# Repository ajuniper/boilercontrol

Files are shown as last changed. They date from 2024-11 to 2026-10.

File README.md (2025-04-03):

# Boiler Controller

ESP32 based heating and hot water controller with LCD touchscreen, RTC, web page, temperature sensors for boiler cycling.

Being created to try to make an aging oil boiler more efficient with different target temperatures for different circuits, with setback based on outside temperature, with cooldown cycles to use the heat left in the system when the schedule is completed.
More description, photos and screenshots coming soon.

## URLs

All requests are `GET` requests (yuk!)

* `/` and `/boiler` gives current status and management controls

* `/scheduler` gives html page for setting schedules
* `/schedset?ch=X&day=D&slot=H:MM&state=01` for updating individual slots in schedules, day = 0-6=M-S, state = 0 or 1
* `/schedset?ch=X&day=D&slot=H:MM` retrieve given schedule slot
* `/schedset?ch=X&day=D` retrieve schedule for day
* `/config?name=schedule&id=N&value=X` set schedule for channel N, must be 96 0/1/2 characters

* `/heat?ch=N&q=X` manual timer for channel, where X is seconds to run (0=off, -1=forever)
* `/config?name=chactive&id=N&value=X` set channel active or inactive

* `/config?name=wuBase&id=N&value=X` set time channel starts before requested on time
* `/config?name=wuThrsh&id=N&value=X' set temp below which channel N will start early
* '/config?name=wuScale&id=N&value=X' set float scaling factor to calculate advance time from amount below threshold
* '/config?name=wuLimit&id=N&value=X' set max amount channel can advance by

* '/config?name=bstThrsh&id=N&value=X' set temp below which channel N will switch to boosted temperature

* `/config?name=orThrsh&id=N&value=X' set temp below which channel N will finish late
* '/config?name=orScale&id=N&value=X' set float scaling factor to calculate overrun time from amount below threshold
* '/config?name=orLimit&id=N&value=X' set max amount channel can extend by

* `/config?name=tgttmp&id=N` reports current target hot temperature for channel N
* `/config?name=tgttmp&id=N&value=X` sets target hot temperature for channel N
* `/config?name=tgttmp2&id=N` reports current target warm temperature for channel N
* `/config?name=tgttmp2&id=N&value=X` sets target warm temperature for channel N
* `/config?name=cooltmp&id=N&value=X` sets min cooldown temperature for channel N
* `/config?name=coolrun&id=N&valueX` sets the cooldown run time for channel N (default 120, 0 = off)
* `/config?name=circtime&id=N&valueX` sets the sludge buster max time to sit idle in seconds (default 86400 = 1 day, 0 = off)
* `/config?name=circrun&id=N&valueX` sets the sludge buster run time (default 120, 0 = off)
* `/config?name=mainsthrsh&id=N&valueX` sets the mains detection threshold for pin N (default 350, pins 34, 35 ,36, 39 )

* `/config?name=boiler&id=cyct&value=X` sets min off time for cycling boiler (default 120 seconds)
* `/config?name=boiler&id=cycpc&value=X` sets percentage which flow must drop to end cycle (default 10%)
* `/config?name=boiler&id=wait&value=X` sets time in S to wait after setting each relay (3 seconds)

* `/config?name=showbutt&id=0&value=X` enable or disable showing button regions, 1=regions+touch, 2=regionsboxed+touch, 3=2+syslog touch

Provided by the updater library:
* `/update` gives page for doing OTA updates
* `/update` use __POST__ request with body containing new firmware.bin
* `/reboot` reboots the system

Provided by tempreporter library:
* `/temperatures` reports current DS18B20 readings
* `/api?id=XXX` reports current temperature for sensor named `XXX`
* `/config?name=trremap&id=X&value=AAA+NNN+DIS` sets name of sensor `AAA` to `NNN` (where `XXX` is typically sensor MAC address), optionally disables
* `/fake?id=XXX&temp=t.tt` creates fake sensor `XXX` with value `t.tt` (used for testing)
* `/config?name=trpin&id=(18b20|dht11)[&value=N]` sets or gets the pin associated with the different sensors (reboot after to take effect)

Provided by the tempfetcher library
* `/config?name=fcst&id=rate&value=X` sets the minutes between fetching forecasts
* `/config?name=fcst&id=ahead&value=X` sets the number of hours ahead to look for lowest temperature
* `/config?name=fcst&id=behind&value=X` sets the number of hours behind to look for lowest temperature
* `/config?name=weather&id=url&value=x` sets the URL to retrieve weather forecasts from

## Expected sensor names

Need to associate specific DS18B20 with given name via the `/remap` URL above.
Max 12 characters due to preferences library limits.

* `boiler.flow` is the sensor on the output from the boiler
* `boiler.rethw` is the sensor on the return from the hot water tank
* `boiler.retht` is the sensor on the return from the main heating circuit

## Preferences objects

pin.ds18b20
pin.dht11
remap.[sensorID]
temprep.poll
temprep.submit

wifi.hostname
wifi.ssid
wifi.password

targettemp.[ch]
chactive.[ch]
warmup.[ch]
schedule.[ch]

## Scheduler web page DOM objects

* channels tabs
* days tabs
* c0 c1 (chcontent)
  * s0.0 s0.1 s0.2 ... (daycontent)
    * form (schedule)
      * 00:00 (timeslot)
      * label
        * checkbox value="hh:mm"
      * label
        * checkbox value="hh:mm"
      * label
        * checkbox value="hh:mm"
...

## configuring temperature sensors
```
curl -s 'http://boiler/config?name=trremap&id=0&value=28-ff641f79b51c46+boiler.flow+1'
curl -s 'http://boiler/config?name=trremap&id=1&value=28-ff641f79b7e8c2+boiler.rethw+1'
curl -s 'http://boiler/config?name=trremap&id=2&value=28-ff641f79b7d4df+boiler.retht+1'
```

## My House Settings

### Boiler

Extend zone valve duration a little beyond default
```
boiler.cyct = 120
boiler.cycpc = 10
boiler.wait = 5
fcst.ahead = 5
```

### Hot Water

No warm up time to be added

```
wuBase = 0
```
Advance if 0 degrees in forecast by up to 15 minutes
```
wuThrsh = 0
wuScale = 180
wuLimit = 900
```
No boost or overrun
```
bstThrsh = -100
orThrsh = -100
orScale = 0
orLimit = 0
```
Target temperature 65 degrees, only one run temperature
```
tgttmp = 65
tgttmp2 = -1
```
Only run cooldown cycle for 3 minutes or until less than 60 degrees
```
cooltmp = 60
coolrun = 180
```
Circulate daily for a minute for sludge buster
```
circtime = 86400
circrun = 60
```

### Heating

Heating always needs 45min warmup
```
wuBase = 2700
```
Extend heating by up to an hour if forecast less than 8 degrees (extra 4 minutes per degree)
```
wuThrsh = 8
wuScale = 240
wuLimit = 3600
```
Force heating hot if less than -3 degrees forecast
```
bstThrsh = -3
```
Extend heating by up to half an hour if forecast less than -3 (extra 3 minutes per degree)
```
orThrsh = -3
orScale = 180
orLimit = 1800
```
Temperatures are 50 and 65 degrees
```
tgttmp = 65
tgttmp2 = 50
```
Overrun until boiler temp is 45 or for 15 minutes
```
cooltmp = 45
coolrun = 900
```
Circulate daily for 2 minutes for sludge buster
```
circtime = 86400
circrun = 120
```

## Config backup

```
curl -s 'http://boiler/configlist' | while read a b ; do [[ $a = myconfig/* ]] || continue ; c="${a/./\&id=}" ; c="${c/myconfig\//http:\/\/boiler/config?name=}" ; v=$(curl -s "$c") ; echo "curl -s \"$c&value=$v\"" ; done

```

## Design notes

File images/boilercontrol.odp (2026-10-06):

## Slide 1

http://boiler.local/

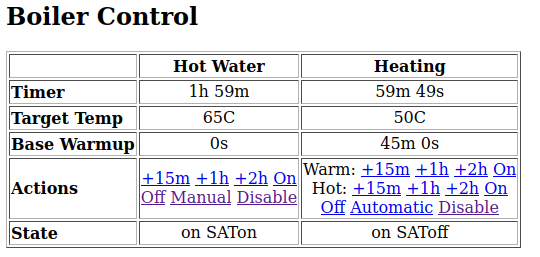
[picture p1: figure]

Time left to run

- Add 1/2/3 hours extra time
- For heating pick warm or hot
- Off will stop now but continue with next schedule
- Manual stops scheduling
- Automatic enables scheduling
- Disable turns it off completely (e.g. going away)

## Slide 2

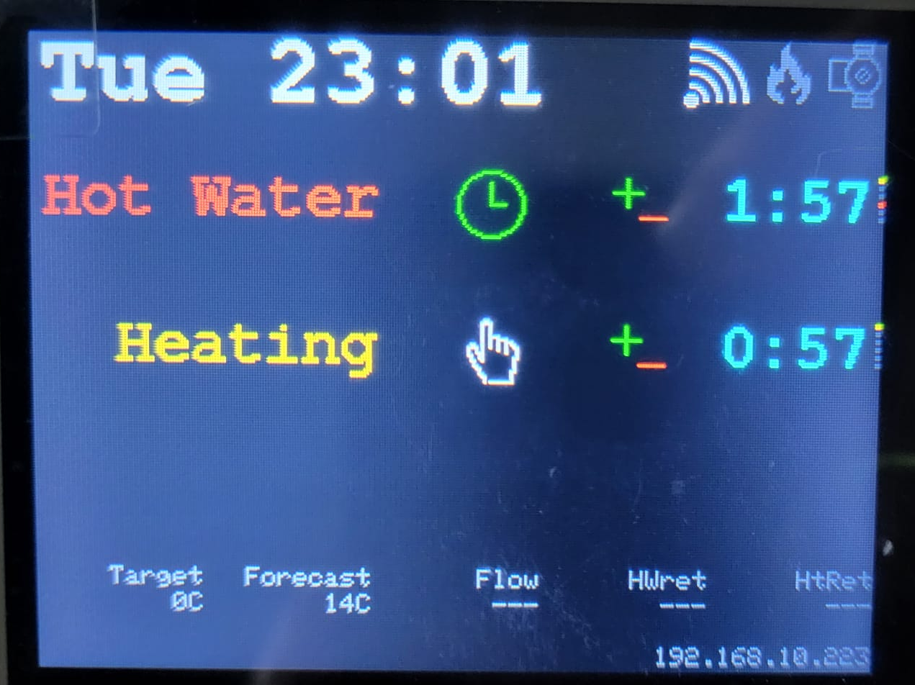
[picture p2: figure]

Enable/disable

(e.g. on holiday)

Clock = automatic

Hand = manual

No Entry = off

Orange = Low temp

Red = High temp

(set before time)

Touch and release to add 1 hour

Press and hold to turn off

Boiler and Pump

Grey = off

Blue = cooling

Red = on

Remaining time

Display goes off after 30s, touch to wake it again

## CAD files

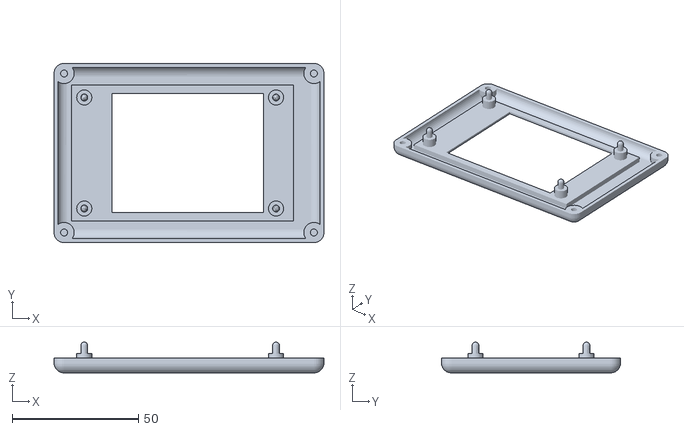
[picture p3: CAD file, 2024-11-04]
images/bezel.stl
107.0 x 71.0 x 12.2

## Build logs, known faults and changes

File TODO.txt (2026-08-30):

TEST
. coredump copy to FFS
. coredump download to set save as filename
. on/off -> off / manual / automatic
. scheduler to look at bank holidays
  https://www.gov.uk/bank-holidays.json
  https://date.nager.at/scalar/#api-version-3/tag/publicholiday/GET/api/v3/IsTodayPublicHoliday/{countryCode}
  https://date.nager.at/Api/v3/IsTodayPublicHoliday/IN?countyCode=KA
  https://api.bigdatacloud.net/data/reverse-geocode-client?latitude=51.75413&longitude=-1.124867&language=en
  https://ip-api.com/docs  http://ip-api.com/csv/?fields=countryCode,region

WIP
. add forecast lookback

FIX
. ignore input signals if corresponding output inactive
  . false triggers of ready flags
. work out how to ignore powerline noise
. wifi watchdog to restart if heating idle
  . what is behaviour of wifi reconnect?  do we get a further disconnected event?
. syslog buffer if offline
. sort PSU plug
. fix segvs
  . heating is on add hw - brownout?
  . heating is cooldown add hw - temporarily end up with not heating, not hw, pump is on
  . reduce stack sizes
  . add esp and arduino versions to /status
  . switch out syslog library
. copy-to-next does not unset existing values
. scheduler web page should cycle off warm off hot
. scheduler web page should show warmup parameters

. web show more config values
. should boost during warmup consider flow/return temp?
. should forecast tracker look at highs as well?

TODO
. button to reboot
. scheduler move day selector to LH column
. add schedule profiles
. add "if forecast temp is above X do not run"
. make web look like lcd
. scheduler onscreen
. adjust target temp based on return temp (what are the rules?  try to minimise flow based on ret+15?)
. auto hotspot if no wifi
. ntp, syslog targets from dhcp
. mqtt

IGNORE wnf
. persist on-until time in rtc/flash (scheduler fixes)
. run heating hotter for some initial period (do it manually via multi temp schedule)
# query param to avoid redirect on direct config change (new value in 302)
. watchdog timer (already there)
* target temp defaults to 0
# when web sets warm/hot, display should update
. save default config values

TESTED
rtc integration
target temperature adjustment
temperature cycling
web server
pump/boiler icon colour
1h displayed as 1:60
pump stays blue after channels go off
fake temperatures
. web
        . need newline before Hot Water 1h
        . obey channel enabled flag
        . add control for enable
. why does pump run on when HW satisfied? (icon only)
. flash persistence
. timezone not in effect
. scheduler page does not render due to JS error
. littlefs fails to open/initialize every time
. save channel active setting in flash
scheduler
    scheduler does not save to flash
    scheduler js does not load from boiler
    initialiser to read from flash
    URL to set 15 minute slot
    scheduler method to set slot & save to flash
    scheduler to obey channel active flag
    copy-to-next button
    done button
    web page to set schedule with js for toggling
link to scheduler from front page
. copy to next Sat->Sun does not work
. crashes when using copy to next / switching day
. scheduler js should use one get not 96
    bulk load of daily schedule
    correct runtime if turn on in middle of HW cycle
    URL to adjust base warmup
    scheduler does not account for time slot already partially passed
    summertime heating cycling (30s every 10 mins)
    scheduler warmup set
    correctly detect heating if turn on <warmup before schedule
. why does web say heating satisfied + satisfiedON?
. web links ok after becoming relative
. stop button should inhibit scheduler until end of current cycle
. run scheduler at reboot
. sludge buster should not run if this channel active
    sludge buster will start @5 mins
    start manual timer to overlap with sludge buster
. check scheduler behaviour if channel ready running ( for < or > time)
. web page runtime/cooldown time should be hh:mm:ss not just /60
. sludge buster should not run if other channel active (should not leave channel on off/calls/satoff)
. check uptime
. sat output should record/report state even if no pin
. changing schedule should force reevaluation
# temp labels
# invert touch screen coordinates if display_rotation=3
# target should be --- if boiler off
# fake temperatures
# mains sense inputs in reverse order
# relay outputs in wrong order
# cycle based on flow hysteresis + min cycle time
# config for boiler cycling
# config to disable tempreporter
display to show target temp
temperature fetching
. web rotate top table to show better on mobile
. test /configlist
. check display updates as expected on turn-off
# active does not load from config / save to config
# scheduler config names not documented
# schedule does not load from config / save to config (rejected by mycfg)
  (maybe try putData / getData or RLE)
# tempreporter remap config names too long
# scheduler config nodes name too long
# set full schedule to config causes segv (add printf)
. scheduler done link does not go back to home page
# lcd active does not save to config
. watchdog reboots when first starting - TR task - fixed?
. clock refresh flicker
# no clock until wifi joined
. rewire mains to boiler correctly
. relay #4 not working, LED not active
. all relays work
. if start hw then htg, htg relay does not fire
. test html pages
tempchannel to have multiple temps
        know which is in use - scheduler
        know which is in use - web
        know which is in use - display
        know temp for each
. sequence with delay boiler off, pump off, zv deactivate - not all changed in single pass, cannot deactivate zv before pump
  . test changes to sequence boiler and pump on
. weird syslog characters
. config value for 3s delay
. config for sludge buster
. test state info always present in web even if ch disabled
. if shorten schedule then need to recalculate
. if turn off during schedule then do not restart until next interval
. cycle based on return temp + min off time
. heating boost   bstThrsh(0)
. extend manual heating via web does not update target temp
tempchannel to have multiple temps
        scheduler to spot change in requested temp and adjust
. heating advance wuThrsh(12) wuScale(0) wuLimit(0)
. defer sludge if other channel is active
. heating extend  orThrsh(4) orScale(0) orLimit(0)
. when load schedule page, select current day
. refresh web page every 15s
. sludgebuster should run for shorter time than cooldown
. cooldown based on temperature
. cooltime != circtime, during circ do not check temperature
. config value for mains detect threshold
. boost temperature during warmup
. calibrate mains detectors
. adjustTimer to ignore small changes
. touch screen flaky - reflow header on LCD
. config value for mains detect INPUT_ON_MILLIS
. check ready pin behaviour states
. check that mainsdetect is happy with half wave from mid position setting
. add +15m option to web
. add status web page showing bssid, cpu%, ram, etc.
. save core dumps to flash and serve via web
. correctly pick best SSID at boot
. force reset 1wire bus if no sensors - how?
. query DS18B20 individually to make compatible with parasitic mode
. move internal cables away from display
. coredump copy to FFS
. coredump download to set save as filename

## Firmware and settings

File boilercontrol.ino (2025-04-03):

#include <mywifi.h>
#include "projectconfig.h"
#include <AsyncTCP.h>
#include "time.h"
#include <WiFiUdp.h>
#include <mysyslog.h>
#include "pinconfig.h"
#include "display.h"
#include "tempsensors.h"
#include "mytime.h"
#include "outputs.h"
#include <tempreporter.h>
#include <mywebserver.h>
#include <webupdater.h>
#include <myconfig.h>
#include "scheduledoutput.h"
#include "buttons.h"
#include <mysystem.h>

// task to update outputs
static TaskHandle_t outputtask_handle = NULL;

// last output state
ScheduledOutput o_pump_on;
ScheduledOutput o_boiler_on;
t_output_state o_boiler_state;
t_output_state o_pump_state;
int target_temp = 999;

#include <my_secrets.h>
const char* ssid     = MY_WIFI_SSID;
const char* password = MY_WIFI_PASSWORD;

// if we cycle the boiler off at its target temperature
// then we can't start it again for this period
#ifdef SHORT_TIMES
#define BOILER_SHORT_CYCLE 30
#else
#define BOILER_SHORT_CYCLE 120
#endif
#define BOILER_RELAY_WAIT 3

//////////////////////////////////////////////////////////////////////////////
//
// Heat channel objects
#include "heatchannel.h"

//////////////////////////////////////////////////////////////////////////////
//
// Web Server Stuff
#include "webserver.h"

static const char * handleConfigBoiler(const char * name, const String & id, int &value) {
    if (id == "cyct") {
        // all ok, save the value
        return NULL;
    } else if (id == "cycpc") {
        // all ok, save the value
        return NULL;
    } else if (id == "wait") {
        // all ok, save the value
        return NULL;
    } else {
        return "boiler config not recognised";
    }
}


//////////////////////////////////////////////////////////////////////////////
//
// setup

void setup() {
    // put your setup code here, to run once:
    // Serial port for debugging purposes
    Serial.begin(115200);
    Serial.println("Starting...");
    MyCfgInit(true);
    MyCfgRegisterInt("boiler", &handleConfigBoiler);

    mytime_setup(MY_TIMEZONE, PIN_RTC_CLK, PIN_RTC_DATA, PIN_RTC_RST);
    WIFI_init("boiler");
    SyslogInit("boiler");
    xTaskCreate(output_task, "outputs", 10000, NULL, 1, &outputtask_handle);
    webserver_setup();
    SYS_init();
    tempsensors_init();
    heatchannel_setup();
    buttons_init();

    // start the display update task
    display_init();

    // firmware updates
    UD_init(server);
}

//////////////////////////////////////////////////////////////////////////////
//
// output control
// separate task to permit mains cycle sync

static void output_task (void *)
{

    // set up digital IO - set output state before setting mode to avoid boot time glitches
    digitalWrite(PIN_O_PUMP_ON, RELAY_OFF);
    digitalWrite(PIN_O_BOILER_ON, RELAY_OFF);
    pinMode(PIN_O_PUMP_ON, OUTPUT);
    pinMode(PIN_O_BOILER_ON, OUTPUT);

    delay(1000);

    // cache the requested output settings
    // only update when we are signalled
    bool last_boiler = false;
    bool this_boiler = false;
    bool this_pump = false;
    int last_target_temp = target_temp;
    time_t boiler_cycle_time = 0;
    int hysteresis = 100 - 10;
    int i;
    bool need_suspend = false;
    bool last_suspend;

    while(1) {
        // wait for signal
        uint32_t n = 0;
        while (n == 0) {
            TickType_t waittime = 5*1000; // 5s
            time_t now = time(NULL);
            int flow_temp = tempsensors_get("boiler.flow");

            this_boiler = o_boiler_on.checkState(now);
            if (last_boiler != this_boiler) {
                if (this_boiler == true) {
                    syslogf(LOG_DAEMON | LOG_WARNING, "Boiler can fire, temp now %dC",tempsensors_get("boiler.flow"));
                }
                last_boiler = this_boiler;
                boiler_cycle_time = 0;
            }

            last_suspend = need_suspend;
            need_suspend = false;
            for (i=0; i<num_heat_channels; ++i) {
                need_suspend |= channels[i].isChanging(now);
            }
            if (need_suspend != last_suspend) {
                if (need_suspend) {
                    syslogf(LOG_DAEMON|LOG_WARNING, "Suspending pump and boiler for valve change");
                } else {
                    syslogf(LOG_DAEMON|LOG_WARNING, "Resuming pump and boiler after valve change");
                }
            }

            // recalculate whether the boiler should be running or not
            // this is where we are cycling the boiler to temperature
            if (this_boiler == false) {
                // boiler is requested off
                boiler_cycle_time = 0;
                waittime = 3600 * 1000; // 1hr
                o_boiler_state = OUTPUT_OFF;

            } else if (need_suspend) {
                // zone valves are changing, we should turn pump and boiler off
                waittime = 1000; // 1s
                o_boiler_state = OUTPUT_OFF; // OUTPUT_SUSPEND
                this_boiler = false;
            } else if (boiler_cycle_time > now) {
                // boiler is already cycled off by time so nothing to do
                // just wait until the end of the cycle window unless
                // something changes in the mean time
                waittime = (boiler_cycle_time - now) * 1000;
                this_boiler = false;

            } else if ((boiler_cycle_time != 0) &&
                       (flow_temp > ((last_target_temp * hysteresis)/100))) {
                // boiler is cycled off by temperature so nothing to do
                // just wait a few seconds and check again unless
                // something changes in the mean time
                waittime = 10000;
                this_boiler = false;

            } else if (flow_temp > last_target_temp) {
                // boiler just went over temperature

                // read the cycling config
                int short_cycle = MyCfgGetInt("boiler","cyct", BOILER_SHORT_CYCLE);
                hysteresis = 100 - MyCfgGetInt("boiler","cycpc", 10);

                syslogf(LOG_DAEMON | LOG_WARNING, "Cycling boiler off, flow temp %dC is greater than target %dC fire again at %dC",flow_temp,last_target_temp,((last_target_temp * hysteresis)/100));

                // start a new cycle period
                this_boiler = false;

                // the earliest time the boiler can fire again
                boiler_cycle_time = now + short_cycle;

                // how long to wait before looking again
                waittime = short_cycle * 1000;

                // we are cycling the boiler
                o_boiler_state = OUTPUT_COOLING;

            } else {
                // boiler should be on
                o_boiler_state = OUTPUT_HEATING;
                if (boiler_cycle_time != 0) {
                    // boiler just finished cycling
                    syslogf(LOG_DAEMON | LOG_WARNING, "Cycling boiler back on, temp now %dC",flow_temp);
                    boiler_cycle_time = 0;
                }
            }

            // calculate what the pump should be doing
            if (need_suspend) {
                // pump should be off for zv change
                this_pump = false;
                o_pump_state = OUTPUT_OFF; // OUTPUT_SUSPEND
            } else if (o_pump_on.checkState(now)) {
                this_pump = true;
                // update what the pump is doing
                // if boiler is on or cycling then we are heating
                o_pump_state = (o_boiler_state == OUTPUT_OFF)?OUTPUT_COOLING:OUTPUT_HEATING;
            } else {
                // pump is not on
                this_pump = false;
                o_pump_state = OUTPUT_OFF;
            }

            // update the outputs
            digitalWrite(PIN_O_PUMP_ON, this_pump?RELAY_ON:RELAY_OFF);
            digitalWrite(PIN_O_BOILER_ON, this_boiler?RELAY_ON:RELAY_OFF);

            for (i=0; i<num_heat_channels; ++i) {
                if (channels[i].setOutputPin(now)) {
                    waittime = min((TickType_t(500)), waittime);
                }
                if (channels[i].setSatisfiedPin(now)) {
                    waittime = min((TickType_t(500)), waittime);
                }
            }

            // if change is coming then be ready for it
            if (o_boiler_on.nextChange() > 0) {
                waittime = min((TickType_t(500)), waittime);
            }
            if (o_pump_on.nextChange() > 0) {
                waittime = min((TickType_t(500)), waittime);
            }
            // wait for something to change, either demand state or
            // calculated time period elapsed
            n = ulTaskNotifyTake( pdTRUE, pdMS_TO_TICKS( waittime) );

            // n==0 indicates timeout, else signalled
        } // end of wait for signal/timeout

        // drop out of loop if signalled that demand state changed
        last_target_temp = target_temp;
        if (last_target_temp == 999) { last_target_temp = 0; }
    }
}

//////////////////////////////////////////////////////////////////////////////
//
// main loop

void loop() {
    time_t now = time(NULL);
    unsigned long millinow = millis();
    bool changed = false;
    int i;
    BaseType_t xHigherPriorityTaskWoken = pdFALSE;

    // check timers
    for(i=0; i<num_heat_channels; ++i) {
        if (channels[i].updateTimers(now,millinow)) {
            changed |= true;
            syslogf(LOG_DAEMON|LOG_INFO,"%s triggered change",channels[i].getName());
        }
    }

    if (changed) {
        bool calling = false;
        target_temp = 0;

        // cache the interval between relay changes
        time_t relaywait = MyCfgGetInt("boiler","wait", BOILER_RELAY_WAIT);

        // see what is ready for action
        for (i=0; i<num_heat_channels; ++i) {
            if (channels[i].wantFire()) {
                calling |= true;
            }
        }
        // 999 is rendered as --- on the display
        if (target_temp == 0) { target_temp = 999; }
        if (calling) {
            // something is calling for heat
            int tt = 0;

            // action the ZV relays
            // if we get to this loop then something IS calling for fire
            // cool down is not possible if something is calling for fire
            // TODO temporary disable pump and boiler while relays change
            // TODO can we detect change in progress by output != input?
            for (i=0; i<num_heat_channels; ++i) {
                // we must set satisfied to indicate to not send heat to this channel
                // if the channel is satisfied or this channel is not asking for heat
                // (which can include cooldown too)
                // these changes are start-of-sequence so happen immediately
                bool satNew = (!channels[i].canFire()) || channels[i].isSatisfied();
                bool runNew = channels[i].wantFire();
                // sequence the requests so that we do not have a temporary contradiction
                // must not have both sat and run set
                // if sat is turning on and we are already running then turn off run first
                // and vice versa
                if (satNew) {
                    // must turn run off first
                    channels[i].setOutput(runNew,now+1);
                    channels[i].setSatisfied(satNew,now+2);
                } else {
                    // must turn sat off first
                    channels[i].setSatisfied(satNew,now+1);
                    channels[i].setOutput(runNew,now+2);
                }
            }

            // turn the pump and boiler on as required
            for (i=0; i<num_heat_channels; ++i) {
                if (channels[i].wantFire()) {
                    syslogf(LOG_DAEMON|LOG_INFO,"%s is ready",channels[i].getName());
                    // have to wait for ack from zv before firing
                    if (channels[i].canFire()) {
                        // something is asking for heat
                        tt = max(tt, channels[i].targetTemp());
                        // give the pump and boiler time for the zv to be in place
                        o_pump_on.setState(true, now+relaywait);
                        o_boiler_on.setState(true,now+relaywait+relaywait);
                        syslogf(LOG_DAEMON | LOG_WARNING, "Run pump and boiler to %dC",tt);
                    }
                }
            }
            target_temp = tt;

        } else {
            // nothing asking for heat, what about cooldown?
            calling = false;
            for (i=0; i<num_heat_channels; ++i) {
                if (channels[i].wantCooldown()) {
                    calling |= true;
                }
            }

            if (calling) {
                // something is asking for cooldown
                // this ensures other ZVs are closed

                // action the ZV relays
                // if we get to this loop then something IS calling for cooldown
                // and nothing is calling for heat
                // TODO temporary disable pump and boiler while relays change
                for (i=0; i<num_heat_channels; ++i) {
                    // we must set satisfied to indicate to not send heat to this channel
                    // if the channel is satisfied or this channel is not asking for heat
                    // (which can include cooldown too)
                    // these changes are start-of-sequence so happen immediately
                    bool satNew = channels[i].isSatisfied();
                    bool runNew = channels[i].wantCooldown();
                    // sequence the requests so that we do not have a temporary contradiction
                    // must not have both sat and run set
                    // if sat is turning on and we are already running then turn off run first
                    // and vice versa
                    // scrub that
                    // if we are now satisfied then we must enable satisfied to
                    // stop sending hw to tank at mpzv before we close the tank zv
                    // ditto v.v. if we are not satisfied (i.e. want heat to tank)
                    // then we must turn on tank zv to permit flow before we
                    // disable the satisfied output to permit tank flow from mpzv
                    if (!satNew) {
                        // want heat to tank
                        // must turn run off first
                        channels[i].setOutput(runNew,now);
                        channels[i].setSatisfied(satNew,now+1);
                    } else {
                        // do not want heat to tank
                        // must turn sat off first
                        channels[i].setSatisfied(satNew,now);
                        channels[i].setOutput(runNew,now+1);
                    }
                }

                // and set the pump/boiler
                // boiler defaults to off anyway, pump should already be on
                for (i=0; i<num_heat_channels; ++i) {
                    if (channels[i].wantCooldown()) {
                        syslogf(LOG_DAEMON|LOG_INFO,"%s is ready for cooldown",channels[i].getName());
                    }
                }

                syslogf(LOG_DAEMON | LOG_WARNING, "Run pump for cooldown");
                o_boiler_on.setState(false);
                o_pump_on.setState(true,now+relaywait);
            } else {
                // nothing on

                o_boiler_on.setState(false);
                // give the boiler a chance to stop before stopping the pump
                o_pump_on.setState(false,now+relaywait);

                // action the satisfied relays to off, not needed
                int d=0;
                for (i=0; i<num_heat_channels; ++i) {
                    channels[i].setSatisfied(false,now+relaywait+relaywait+(d++));
                }

                // action the zone valves to off
                for (i=0; i<num_heat_channels; ++i) {
                    channels[i].setOutput(false,now+relaywait+relaywait+(d++));
                }

                syslogf(LOG_DAEMON | LOG_WARNING, "Pump and boiler off");
            }
        }

        // set system outputs - via task to deal with mains sync
        // TODO should setting outputs be synchronised with setting outputs
        xTaskNotifyGive( outputtask_handle );

    } // end of something changed

    // wait a while
    delay(50);
}

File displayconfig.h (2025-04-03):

//////////////////////////////////////////////////////////////////
//
// config for display layout and behaviour
#pragma once


#include "projectconfig.h"
#include "time.h"

#ifdef display_conns_on_left
// if connections are on left then
// display (0,0) is bottom right
// touch (0,0) is top right
#define display_rotation 3
#else
// if connections are on right then
// display (0,0) is top left
// touch (0,0) is bottom left
#define display_rotation 1
#endif
#define display_max_x 320
#define display_max_y 240

// coordinate values below assume
// display (0,0) is top left

// millisecods
#define touch_delay 25
// microseconds
#define touch_release_debounce 100000
#define fontnum 1
#define clock_font &FreeMonoBold18pt7b
#define clock_x 190
#define clock_y 1
#define clock_colour TFT_WHITE
#define button_expand 10
#define display_sleep 30
#define display_brightness 200

#define channel_font &FreeMonoBold12pt7b
#define channel_x 130
#define channel_y 50
#define channel_spacing 55
#define channel_icon_size 24
#define channel_colour TFT_CYAN
#define channel_colour_hot TFT_RED
#define channel_colour_warm TFT_ORANGE
#define channel_label_x 1
#define channel_label_w channel_x
#define channel_active_x (channel_x + 30)
#define channel_active_w channel_icon_size
#define channel_timer_x (channel_x + 86)
#define channel_timer_w channel_icon_size
#define channel_countdown_x 215
#define channel_countdown_w 98
#ifdef SHORT_TIMES
#define timer_increment 10
#else
#define timer_increment 3600
#endif

#define temp_font nullptr
#define temp_x 64
#define temp_y 210
#define temp_colour TFT_DARKGREY

#define ip_font nullptr
#define ip_x 320
#define ip_y 230
#define ip_colour TFT_DARKGREY

#define pump_x 296
#define pump_y 0
#define pump_w 24
#define pump_h 24
#define pump_colour TFT_RED
#define pump_colour2 TFT_BLUE
#define pump_colour3 TFT_MAROON

#define flame_x 270
#define flame_y 0
#define flame_w 24
#define flame_h 24
#define flame_colour TFT_RED
#define flame_colour2 TFT_BLUE
#define flame_colour3 TFT_MAROON

#define wifi_x 225
#define wifi_y 0
#define wifi_w 45
#define wifi_h 40
#define wifi_colour 0xffff

#define rssi_width 24
#define rssi_height 24
#define rssi_spacing 5
#define rssi_x 246
#define rssi_y 22
#define rssi_deg 45
#define rssi_width 1
#define rssi_direction 225
#define rssi_colour TFT_LIGHTGREY

#define heat_io_x 318
//#define heat_io_x 290
#define heat_io_size 2

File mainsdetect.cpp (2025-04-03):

//////////////////////////////////////////////////////////////////////////////
//
// Mains detection objects
#include <Arduino.h>
#include "projectconfig.h"
#include "mainsdetect.h"
#include <mysyslog.h>
#include "myconfig.h"
#include <map>

// input processing stuff
// debounce interval
#define I_DEBOUNCE 100
// min distance from 0v to treat as "on"
#define INPUT_ON_LIMIT 350
// smoothing for mains frequency - only look for volts for max 1/2 cycle
#define MAINS_HZ 50
#define INPUT_ON_MILLIS (1000/(MAINS_HZ*2))

std::map<int, MainsDetect*> detectors;

static const char * cfg_set_threshold(const char * name, const String & id, int &value) {
    int i = id.toInt();
    std::map<int, MainsDetect*>::iterator j = detectors.find(i);
    if (j == detectors.end()) {
        return "Unknown pin";
    }
    if (strcmp(name, "mainsthrsh") == 0) {
        j->second->setThreshold(value);
    } else if (strcmp(name, "mainsticks") == 0) {
        j->second->setTicks(value);
    } else if (strcmp(name, "mainsdbnc") == 0) {
        j->second->setDebounceT(value);
    } else {
        return "Invalid selector";
    }
    return NULL;
}

static bool need_initialise = true;
static void initialise() {
    need_initialise = false;
    MyCfgRegisterInt("mainsthrsh",&cfg_set_threshold);
    MyCfgRegisterInt("mainsticks",&cfg_set_threshold);
    MyCfgRegisterInt("mainsdbnc",&cfg_set_threshold);
}

MainsDetect::MainsDetect(int a_pin, const char * a_name1, const char * a_name2) :
    m_pin(a_pin),
    m_name1(a_name1),
    m_name2(a_name2),
    m_zerov(-1),
    m_debounce(0),
    m_pinstate(0),
    m_state(false),
    m_disabled(true),
    m_threshold(INPUT_ON_LIMIT),
    m_ticks(INPUT_ON_MILLIS),
    m_debounce_t(I_DEBOUNCE)
{
    //calibrate();
    detectors[a_pin] = this;
}

// calibrate the zero volts level
void MainsDetect::calibrate() {
    m_disabled = true;
    if (m_pin == -1) { return; }
    char t2[100];

    if (need_initialise) {
        initialise();
    }
    m_threshold = MyCfgGetInt("mainsthrsh", String(m_pin), INPUT_ON_LIMIT);
    m_ticks = MyCfgGetInt("mainsticks", String(m_pin), INPUT_ON_MILLIS);
    m_debounce_t = MyCfgGetInt("mainsdbnc", String(m_pin), I_DEBOUNCE);

#ifdef MAINSDETECT_TESTMODE
    m_disabled = false;
    pinMode(m_pin, INPUT);
    sprintf(t2,"input pin %d in digital mode",m_pin);
    Serial.println(t2);
#else
    // calculate the average voltage to determine base level
    int a;
    int j;
    a=0;
    // twice as first pass gives bogus results
    for(j=0; j<(1000/MAINS_HZ); ++j) {
        a+=analogRead(m_pin);
    }
    a=0;
    for(j=0; j<(1000/MAINS_HZ); ++j) {
        a+=analogRead(m_pin);
    }
    // calculate the average
    m_zerov=a/j;
    //sprintf(t2,"Av for pin %d is %d\n",m_pin,m_zerov);
    //Serial.print(t2);
    if (m_zerov < 1500) {
        // not there, disable
        // TODO watch for pin coming back?
        //sprintf(t2,"disabled pin %d zerov %d",m_pin,m_zerov);
        //Serial.println(t2);
    } else {
        m_disabled = false;
    }
#endif
}

// refresh the state of the pin (every millisecond)
void MainsDetect::checkstate() {
    if (m_disabled) { return; }

#ifdef MAINSDETECT_TESTMODE
    // test mode, just do digital read
    // pull DOWN to activate
    if (digitalRead(m_pin)==0) {
#else
    int j = analogRead(m_pin);
    if ((j < (m_zerov-m_threshold)) || (j > (m_zerov+m_threshold))) {
#endif
        // mains is on, reset counter, start debounce if required
        if (m_pinstate == 0) {
            // trigger change check after debounce
            m_debounce = millis();
        }
        m_pinstate = m_ticks;
    } else {
        // mains is off, decrement counter
        if (m_pinstate > 0) {
            m_pinstate--;
            if (m_pinstate == 0) {
                // trigger change check after debounce
                m_debounce = millis();
            }
        }
    }
}

// check for debounce expiry and report if changed
bool MainsDetect::updatepin(unsigned long a_millinow) {
    // sets changed to true if value changed
    if (m_pin == -1) { return false; }
    unsigned long debounce;
    if (((debounce = m_debounce) > 0) &&
        ((a_millinow - debounce) > m_debounce_t)) {
        m_debounce = 0;
        bool x = (m_pinstate > 0);
        if (x != m_state) {
            // only action a change if it changed
            m_state = x;
            syslogf(LOG_DAEMON | LOG_INFO, "%s %s input %s",m_name1,m_name2,m_state?"set":"cleared");
            return true;
        }
    }
    return false;
}

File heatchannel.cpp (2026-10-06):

//////////////////////////////////////////////////////////////////////////////
//
// Heat channel objects
#include <Arduino.h>
#include "projectconfig.h"
#include "pinconfig.h"
#include "heatchannel.h"
#include "displayconfig.h"
#include "display.h"
#include "myconfig.h"
#include <ESPAsyncWebServer.h>
#include "tempsensors.h"
#include "finger.h"

#include <mysyslog.h>

#ifdef SHORT_TIMES
#define HEAT_COOLDOWN 30
#define HEAT_SETBACK 60
#define HEAT_SUSPEND 5
#else
#define HEAT_COOLDOWN 600
#define HEAT_SETBACK (45*60)
#define HEAT_SUSPEND 15
#endif


HeatChannel::HeatChannel(
    int a_id,
    const char * a_name,
    int a_pin_o_zv,
    int a_pin_o_zv_satisfied,
    int a_pin_i_zv_ready,
    int a_pin_i_zv_satisfied,
    int a_target_temp1,
    int a_target_temp2,
    bool a_enabled,
    int a_cooldown_duration,
    int a_cooldown_mintemp,
    int a_y,
    int a_setback
) : m_id(a_id),
    m_name(a_name),
    m_pin_zv(a_pin_o_zv),
    m_pin_zv_satisfied(a_pin_o_zv_satisfied),
    m_ready(a_pin_i_zv_ready,a_name,"ready"),
    m_satisfied(a_pin_i_zv_satisfied,a_name,"satisfied"),
    m_target_temp1(a_target_temp1),
    m_target_temp2(a_target_temp2),
    m_enabled(a_enabled),
    m_active(CHANNEL_OFF),
    m_cooldown_duration(a_cooldown_duration),
    m_cooldown_mintemp(a_cooldown_mintemp),
    m_cooldown_target(0),
    m_sludge_duration(120),
    m_endtime(0),
    m_cooldown_time(0),
    m_zv_output(false),
    m_zv_satisfied_output(false),
    m_changed(true), // trigger output setup first time around
    m_scheduler(*this, a_setback),
    m_suspendUntil(0),
    m_suspend_duration(HEAT_SUSPEND),
    m_y(a_y)

{
    if (m_pin_zv > -1) {
        digitalWrite(m_pin_zv, RELAY_OFF);
        pinMode(m_pin_zv, OUTPUT);
    }
    if (m_pin_zv_satisfied > -1) {
        digitalWrite(m_pin_zv_satisfied, RELAY_OFF);
        pinMode(m_pin_zv_satisfied, OUTPUT);
    }
}

// update timer states
// returns true if something changed
// timer or inputs
bool HeatChannel::updateTimers(time_t now, unsigned long millinow) {
    bool ret = m_changed;
    m_changed = false;
    if ((m_endtime > 0) || (m_endtime == CHANNEL_TIMER_SLUDGE)) {
        if (now > m_endtime) {
            // time to turn off
            const char * c = "";
            if (m_endtime == CHANNEL_TIMER_SLUDGE) {
                if (m_sludge_duration > 0) {
                    m_cooldown_target = -99999;
                    m_cooldown_time = now + m_sludge_duration;
                    c = ", starting sludgebuster";
                }
            } else {
                if (m_cooldown_duration > 0) {
                    m_cooldown_target = m_cooldown_mintemp;
                    m_cooldown_time = now + m_cooldown_duration;
                    c = ", starting cooldown";
                }
            }
            m_endtime = 0;
            m_lastTime = now;
            syslogf(LOG_DAEMON|LOG_INFO,"%s turning off%s",m_name,c);
            ret = true;
        }
    }
    if (m_cooldown_time > 0) {
        if (now > m_cooldown_time) {
            // time to turn off
            m_cooldown_time = 0;
            m_lastTime = time(NULL);
            syslogf(LOG_DAEMON|LOG_INFO,"%s cooldown finished",m_name);
            ret = true;
        } else if (tempsensors_get("boiler.flow") < m_cooldown_target) {
            // cooldown flow is low enough, turn off
            m_cooldown_time = 0;
            m_lastTime = time(NULL);
            syslogf(LOG_DAEMON|LOG_INFO,"%s cooldown finished early",m_name);
            ret = true;
        }
    }
    if (m_enabled) {
        ret |= m_ready.updatepin(millinow);
        ret |= m_satisfied.updatepin(millinow);
    }
    return ret;
}
void HeatChannel::adjustTimer(int dt) {
    switch (dt) {
        case CHANNEL_TIMER_OFF:
            // turn off
            if (m_endtime != 0) {
                // channel is running so set end time to
                // a moment ago
                m_scheduler.turnedOff(m_endtime);
                m_endtime = time(NULL)-1;
            } else if (m_cooldown_time != 0) {
                // channel is already off, cancel cooldown
                m_cooldown_time = time(NULL)-1;
            }
            break;
        case CHANNEL_TIMER_ON:
            // turn on
            m_cooldown_time = 0;
            m_endtime = dt;
            break;
        case CHANNEL_TIMER_SLUDGE:
            // run cooldown cycle to circulate sludge
            // TODO set m_endtime to 1/2 and check for this in updateTimers
            m_cooldown_time = 0;
            m_endtime = dt;
            break;
        default:
            // turn on for given seconds
            m_cooldown_time = 0;
            if (dt < 1000000000) {
                // delta
                if ((m_endtime == 0) || (m_endtime == CHANNEL_TIMER_SLUDGE)) {
                    // currently off so calculate absolute off time
                    m_endtime = time(NULL) + dt;
                } else if (m_endtime == CHANNEL_TIMER_ON) {
                    // noop, already fixed on
                } else {
                    // at some arbitrary value, add the extra time
                    m_endtime += dt;
                }
            } else {
                // absolute value, just save it
                m_endtime = dt;
            }
    }
    syslogf(LOG_DAEMON | LOG_INFO, "%s set to %d",m_name,m_endtime);
    m_changed = true;
    // update the last activity time here to hold off the sludge buster otherwise the sludge
    // buster triggers before the main task stops the burner
    m_lastTime = time(NULL);
}

// set the output state to the zv
// returns true if state changes
bool HeatChannel::setOutput(bool state, time_t when) {
    if ((m_enabled == false ) || (m_pin_zv == -1)) {
        return false;
    }
    bool changed = false;
    if (state != m_zv_output.setState(state,when)) {
        syslogf(LOG_DAEMON | LOG_INFO, "%s request output set to %s at %d",m_name,state?"on":"off",when);
        changed = true;
        needSuspend();
    }
    return changed;
}
bool HeatChannel::setSatisfied(bool state, time_t when) {
    if ((m_enabled == false ) || (m_pin_zv_satisfied == -1)) {
        return false;
    }
    bool changed = false;
    if (state != m_zv_satisfied_output.setState(state,when)) {
        syslogf(LOG_DAEMON | LOG_INFO, "%s request satisfied set to %s at %d",m_name,state?"on":"off",when);
        changed = true;
        needSuspend();
    }
    return changed;
}
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

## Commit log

2023-07-16 assign pin for 1wire
2023-07-16 print --- if temp not available
2023-07-16 get wrapper to find sensor to query
2023-07-16 add target temperature support
2023-07-29 configurable target temperatures
2023-07-30 add cooling cycle support
    fix some race conditions when adjusting timer
    [heatchannel.cpp]
2023-08-05 add done button and copy-to-next
2023-09-26 fix 1h shown as 1h60m
    [heatchannel.cpp]
2023-09-30 update pump colour when pump finished
2023-10-02 add log if fail to init littlefs
    [heatchannel.cpp]
2023-10-13 add updates, fix cycling, fix pump icon
    [boilercontrol.ino]
2023-10-15 fix a load of stuff
    [boilercontrol.ino, display.cpp, displayconfig.h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]
2023-10-17 persist heat channel active to flash
2023-11-05 fix problems
    web and scheduler didnt agree on which is day 0
    fix scheduling issues if scheduled mid slot
    save warmup time to flash
2023-11-11 do not run cooldown if other other channel heating
2023-11-11 maintain satisfied output state if no pin
2023-12-19 switch to use preferences library
2024-03-27 rotate display, add multitemp
    add support for display the other way up
    add support for multiple flow temps by clicking label
2024-03-27 add rotation, fix temp positioning
    [display.cpp]
2024-03-27 rotate display, flow temp select, move temps
2024-03-27 add support for multi temp heat channel
2024-03-31 reverse input pin binding order
    [pinconfig.h]
2024-03-31 improve boiler cycling
    make values configurable
    save values to ram
    fix bugs
    [boilercontrol.ino]
2024-05-14 heatchannel now handles save to config
2024-05-14 shorten config names, setactive saves to cfg
    [heatchannel.cpp, heatchannel.h]
2024-07-06 persist active button changes to flash
2024-09-23 update sample config commands
2024-09-23 add display reset button
2024-09-23 channel enums, reset button, disable zv2
2024-10-01 add config for relay wait, rename misc config
2024-10-11 fix stuff, config for cooldown
    fix extend not working
    auto select today in scheduler
    add config for cooldown duration
    rename cooldown variables
    [heatchannel.cpp, heatchannel.h]
2024-10-14 add cooldown runtime and mintemp
    also fix failure to parse config names
    [heatchannel.cpp, heatchannel.h]
2024-10-17 fix display restart button
2024-11-04 add bezel images
    [bezel.stl]
2024-11-17 add runtime enable for button regions
2025-04-03 remove serial prints
2025-04-03 add support for pump+boiler suspend/resume
2025-04-03 fix api v5 issues
    [display.cpp]
